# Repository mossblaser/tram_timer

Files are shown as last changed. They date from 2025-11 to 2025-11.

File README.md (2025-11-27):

Tram Timer
==========

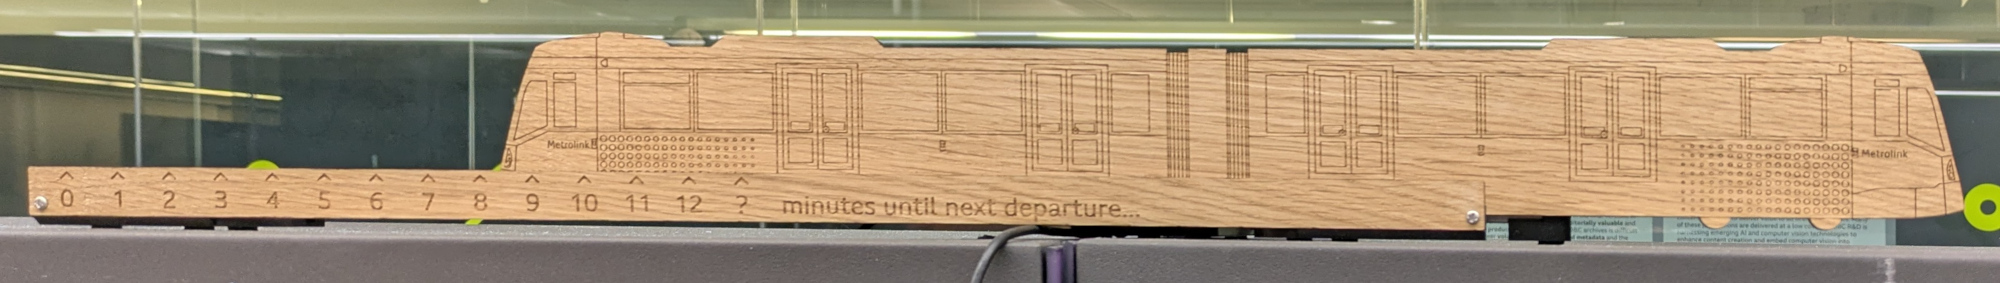
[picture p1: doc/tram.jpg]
A photo of the tram


A model tram which moves along its tracks to indicate how long until the next
departure from a [Manchester Metrolink](https://tfgm.com/ways-to-travel/tram)
tram stop.

Why?
----

There's nothing worse than heading to catch a tram from just outside the office
only to have just missed one, or find one isn't due for ages. Having an
indicator of when the next tram is due means you can always set off at just the
right moment.

This project is the successor to a simple [analogue gauge showing tram
departures I built some years ago](http://jhnet.co.uk/misc/trambox.jpg). Unlike
its predecessor, however, this one can be seen by the whole office.

Design
------

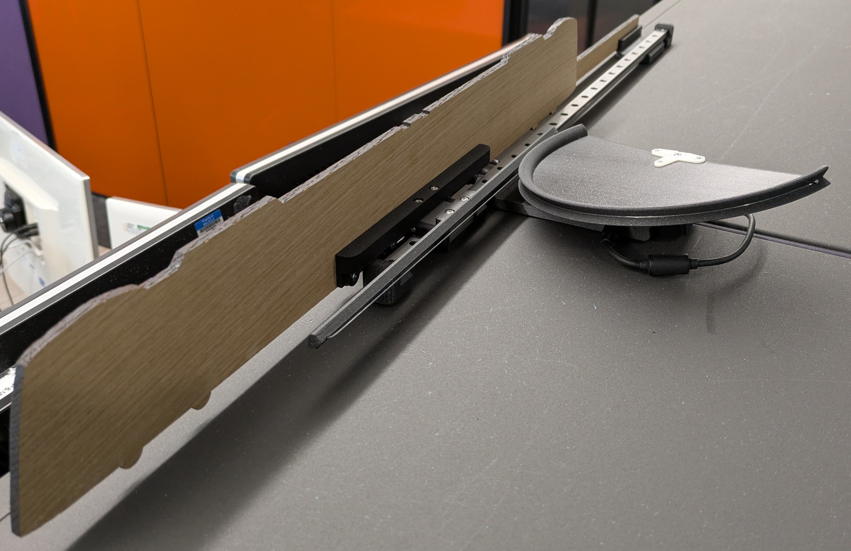
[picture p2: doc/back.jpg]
A photo of the back, showing the mechanism


The mechanism centres around a 600mm MGN12H linear rail (available from the
usual dubious suppliers). A laser cut tram rides along this rail propelled by a
standard RC servo driving a rack-and-pinion style linkage.

A Raspberry Pi Pico W microcontroller pulls Metrolink service data from the
[TFGM/BeeNetwork Metrolink Open Data
API](https://tfgm.com/data-analytics-and-insight/open-data-portal) via WiFi to
drive the servo.

Apart from the laser cut tram and linear rail, all other components are 3D
printed. M-series nuts, bolts and brass heat-set inserts connect everything
together.

### Mechanism

The servo and rack and pinion based mechanism was selected for its extreme
simplicity of implementation. With nothing more than 5v from the USB bus and a
3.3v PWM signal directly from a microcontroller, this setup gets you a
closed-loop absolutely-positioned linear actuator.

Rather than using toothed gears, two lengths of fishing line connect the rack
and pinion. This reduces the need for tight mechanical tolerances and makes
operation quieter.

The major downside of the rack and pinion approach is the additional space
taken up by the pinion wheel. Another limitation is that high resolution
movement accuracy is not typically possible given the slop and dead bands of
typical RC servos.

However, more compact or better performing options such as a belt-driven system
would be unjustifiably more complex to implement for relatively unimportant
gains.

### Firmware

The firmware is "the simplest thing that could possibly work". It's written in
[MicroPython](https://micropython.org/) because performance is utterly
irrelevant and microcontrollers have far too much RAM nowadays.

The only interesting quirk is that the Metrolink API returns status information
for every platform on the entire network in a single large JSON blob too large
to fit in RAM once deserialised. As a result, the firmware must incrementally
read and parse the structure.

For the benefit of future custodians of this device, details on flashing and
configuring the firmware can be found in
[firmware/README.md](./firmware/README.md)

### CAD

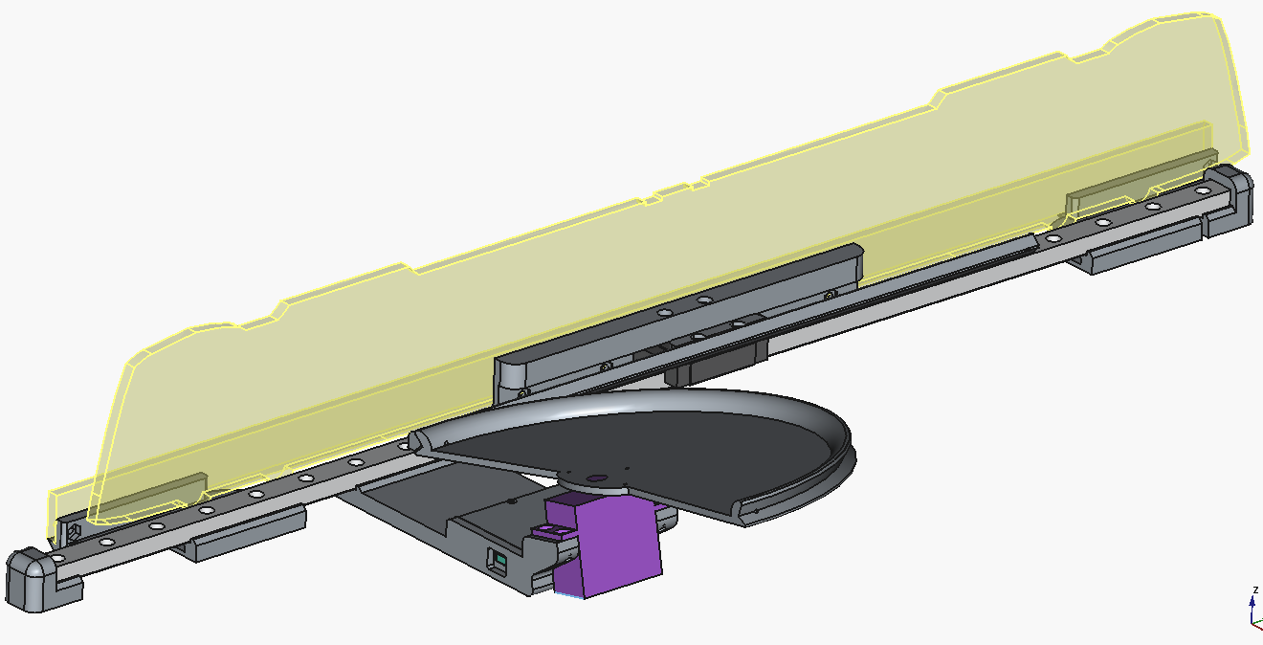
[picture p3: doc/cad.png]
FreeCAD screenshot


This project was my first using FreeCAD 1.0. After dismissing it as unusable
many years ago, I was delighted to discover the hype around FreeCAD 1.0 is
justified. It may be a long way behind its commercial counterparts but it is by
far the most powerful Open Source graphical 3D CAD tool I'm aware of.

2D CAD for the laser-cut tram was, of course, done in Inkscape. For
authenticity, I did most of the work whilst riding the tram.

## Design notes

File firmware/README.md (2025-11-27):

Firmware flashing and configuration
===================================

## Installing MicroPython

To use this firmware, a [MicroPython build for the Raspberry Pi Pico
W](https://micropython.org/download/RPI_PICO_W/) must be installed on the
device. I have tested with v1.26.1. If MicroPython is already installed,
there's likely no need to re-install it -- we just need to update our software.

## Copying the firmware

To copy the firmware onto the device you might wish to use
the [upyt](https://github.com/mossblaser/upyt) tool. Set the device name in
your environment like so:

```sh
export UPYT_DEVICE=/dev/ttyACM0
```

Before we copy anything across, the `config.py` file needs creating and
populating as indicated in `config.py.example`.

> [!NOTE]
> Unfortunately, TFGM/BeeNetwork are not handing out new API keys at the moment
> so you'll need to beg or borrow one.
>
> If you already have a device with an API key configured, make sure you note
> it down (e.g. by reading back the `config.py` file) -- with the key owner's
> permission, of course!
>
>     upyt cp :config.py .

We can fiddle with the `position_min_ns` and `position_max_ns` settings later
on.

Copy the firmware across to the device and reset to set it running:

```sh
upyt sync --reset path/to/firmware/
```

> [!TIP]
> Add the `--terminal` argument to start a serial terminal after the file sync
> is complete.

## Calibrating the servo

Servos can differ slightly in the range of PWM values they expect. To extract
the full range out of a servo, the `position_min_ns` and `position_max_ns`
values may need adjusting. To do this we'll use the MicroPython REPL.

Attach a serial terminal using:

```sh
upyt terminal
```

Since the firmware starts the watchdog timer, we'll need to perform a soft
reset and interrupt the firmware before the watchdog is started. To do this
press Ctrl+D to trigger a reset and then press Ctrl+C during the count-down to
the watchdog starting. You should drop into a Python REPL.

The `tram` object is an instance of the `Tram` class in [`tram.py`](./tram.py).
This is used to move the tram along the track. You can check the calibration by
manually running commands such as:

```python
>>> tram.move_to(4)  # Move to the four minute mark
```

If the spacing is right but everything is offset slightly you might be able to
adjust the position of the countdown board/platform by loosening the screws
attaching it to the linear rail and moving it along.

If the scale is off, you will need to adjust `position_min_ns` and
`position_max_ns`. This is a matter of trying PWM values by trial-and-error for
the '0' and '?' positions on the scale and setting `position_min_ns` and
`position_max_ns` respectively.

To control the servo, first turn it on:

```python
>>> tram._pwm.freq(50)
>>> tram._pwm.duty_ns(566_500)
>>> tram._pwm.init()
```

Then iteratively call `tram._pwm.duty_ns(...)` with new values until you've
determined the two endpoints.

Write the values into `config.py`, copy it onto the device and reset  (using
`upyt sync --reset path/to/firmware/`) and check the calibration again.

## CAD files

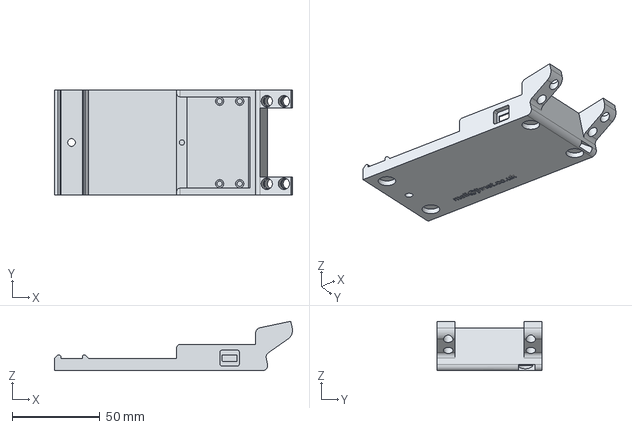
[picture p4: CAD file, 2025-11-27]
cad/3d_print/mechanism-Stand.step
135.5 x 60.0 x 28.2 mm

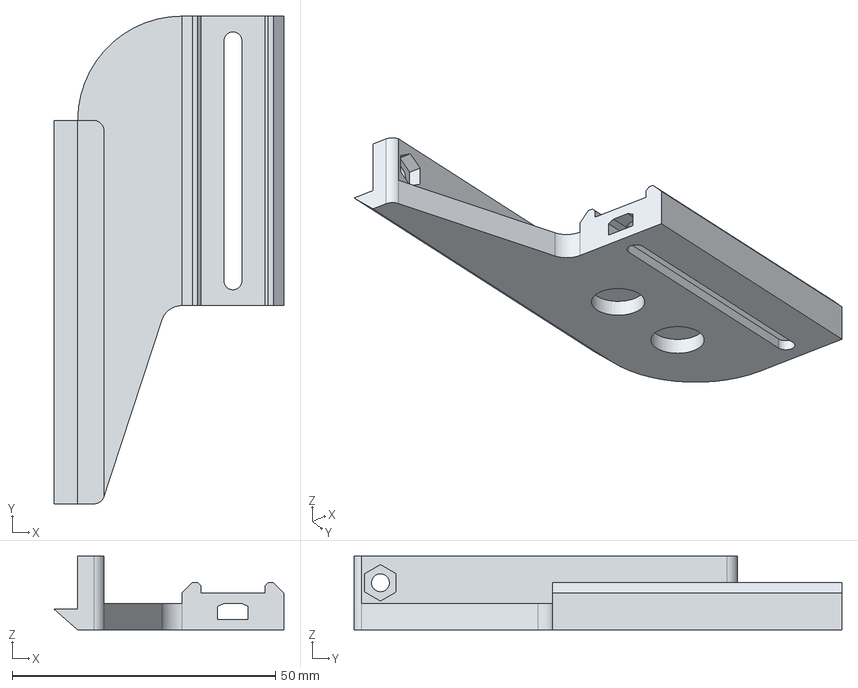
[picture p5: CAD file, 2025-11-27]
cad/3d_print/mechanism-CountdownBracketR.step
43.7 x 92.7 x 14.0 mm

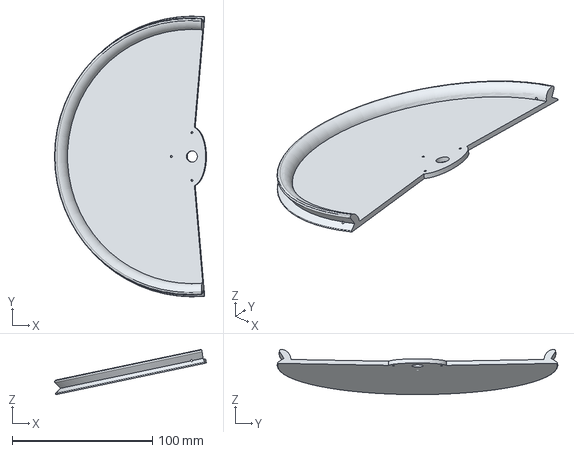
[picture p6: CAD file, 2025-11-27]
cad/3d_print/mechanism-Pinion.step
108.3 x 200.0 x 32.2 mm

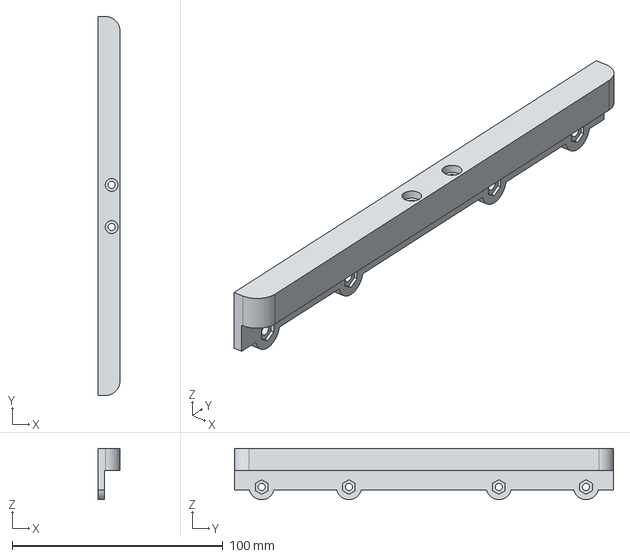
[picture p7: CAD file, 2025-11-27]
cad/3d_print/mechanism-TramCarriage.step
10.5 x 180.0 x 24.3 mm

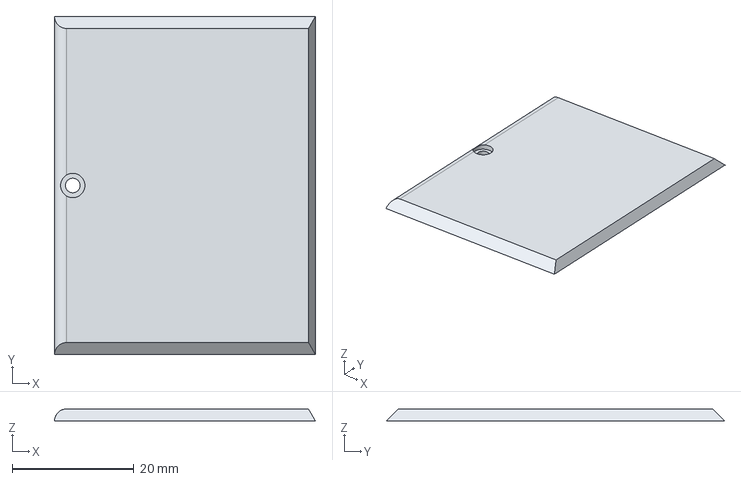
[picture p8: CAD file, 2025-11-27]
cad/3d_print/mechanism-ElectronicsLid.step
42.9 x 55.6 x 2.00 mm

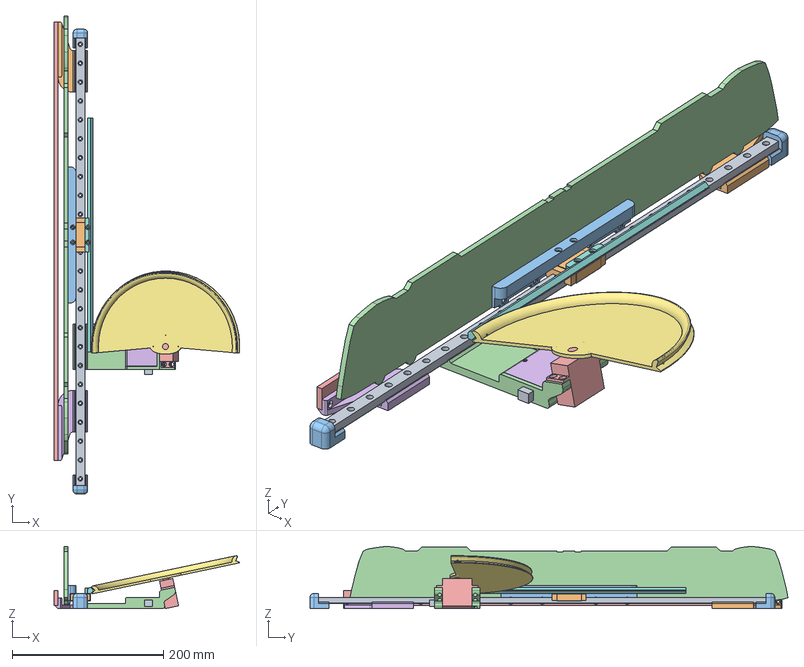
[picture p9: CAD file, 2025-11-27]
cad/3d_print/mechanism.FCStd
245.4 x 632.4 x 82.3 mm
Rail
Block
Foot x 2
Stand
Servo
ElectronicsLid
Pinion
Rack
PicoW
CountdownBracketL
TramCarriage
TramPlaceholder
CountdownPlaceholder
CountdownBracketR

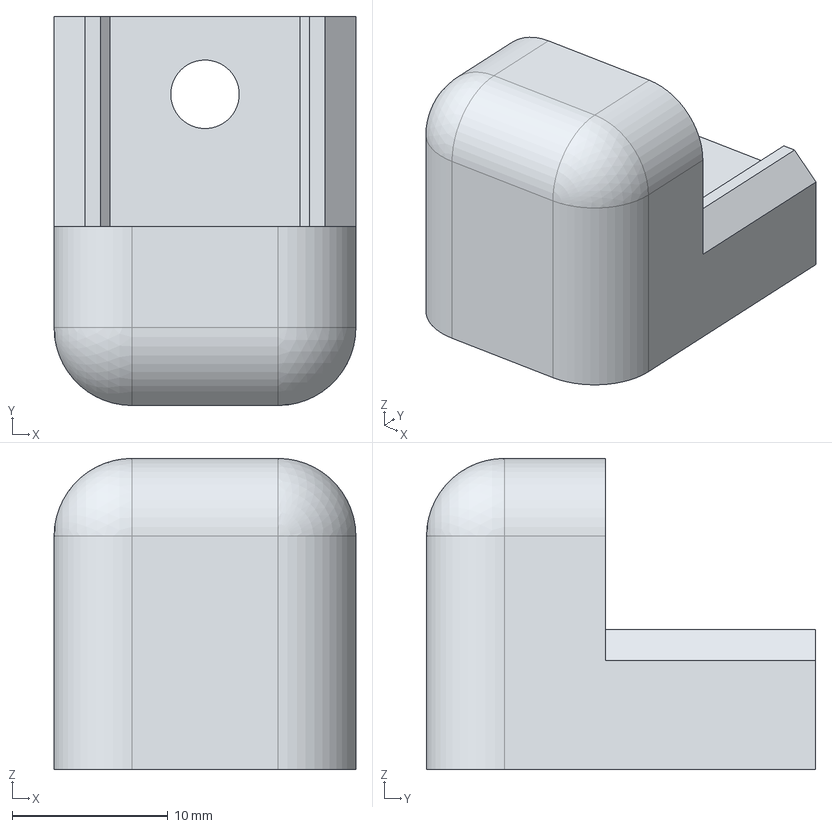
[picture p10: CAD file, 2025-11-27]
cad/3d_print/mechanism-Foot.step
19.4 x 25.0 x 20.0 mm

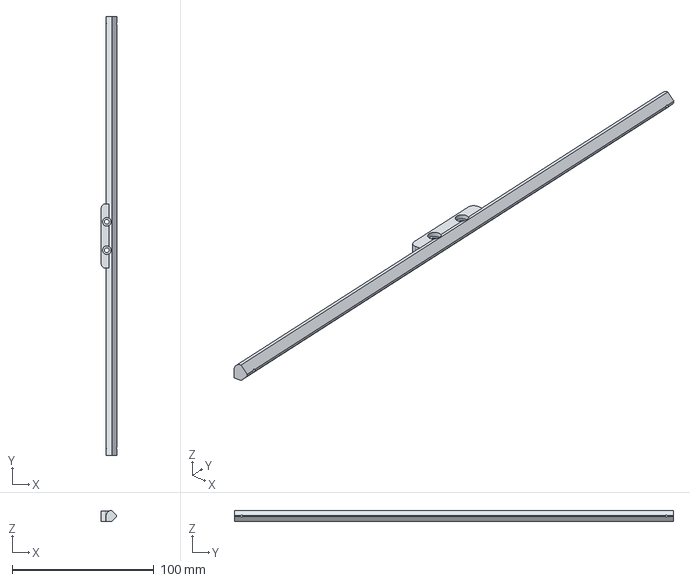
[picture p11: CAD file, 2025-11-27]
cad/3d_print/mechanism-Rack.step
11.0 x 310.0 x 8.00 mm

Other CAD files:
cad/3d_print/mechanism-CountdownBracketL.step

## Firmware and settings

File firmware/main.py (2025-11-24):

import time

from machine import Pin
import network

import watchdog
from tram import Tram
from metrolink_api import get_next_station_departure


if __name__ == "__main__":
    from config import *
    
    pin = Pin(28, Pin.OUT)
    tram = Tram(
        pin,
        position_min_ns=position_min_ns,
        position_max_ns=position_max_ns,
    )
    
    for t in range(10, 0, -1):
        print(f"Starting watchdog in {t}...")
        time.sleep(1)
    watchdog.feed()
    
    print("Connecting to WiFi...")
    nic = network.WLAN(network.WLAN.IF_STA)
    nic.active(True)
    nic.connect(wifi_ssid, wifi_key)
    
    while True:
        try:
            print("Looking up tram times...")
            next_departure = get_next_station_departure(
                station=station,
                excluded_destinations=excluded_destinations,
                api_key=api_key,
            )
            print("Next tram:", next_departure, "min")
            if next_departure is not None and 0 <= next_departure <= 12:
                tram.move_to(next_departure)
            else:
                tram.move_to(13)
            watchdog.feed()
        except Exception as e:
            print("Error:", e)
        finally:
            time.sleep(10)

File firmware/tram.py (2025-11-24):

"""
Implements control of the servo which moves the model tram.

Example:

    >>> from tram import Tram
    >>> tram = Tram(Pin(22))
    >>> tram.move_to(0)
    >>> tram.move_to(5)
    >>> tram.move_to(12)
"""

import math
import time

from machine import Pin, PWM


def sinusoidal_ease(p):
    """
    Simple sinusoidal easing function.
    """
    return -(math.cos(math.pi * p) - 1) / 2

class Tram:
    """
    Controls the movement of the servo which moves the model tram along its
    track.
    
    The tram can move between a defined number of discreete steps defined by
    the 'steps' parameter. Positions are numbered from 0 to steps-1
    (inclusive).
    """

    _pwm: PWM
    
    # The PWM period (in ns) corresponding to minimum/maximum positions
    _position_min_ns: float
    _position_max_ns: float

    # The number of equally-spaced discrete positions the tram can take along
    # its track
    _steps: int
    
    # The last set position of the tram (in steps)
    _position: int | None
    
    # The duration over which a full-scale movement should be performed (in
    # seconds)
    _full_scale_duration: float
    
    # The easing function to use for movements (float -> float)
    _ease: "Callable"

    def __init__(
        self,
        pin: Pin,
        position_min_ns: float = 566_500,
        position_max_ns: float = 2_200_000,
        steps: int = 14,
        full_scale_duration: float = 4.0,
        ease = sinusoidal_ease,
    ) -> None:
        """
        Params
        ------
        pin : Pin
            The pin the servo control pin is attched to.
        position_min_ns : int
        position_max_ns : int
            The servo PWM 50 Hz 'high' period in nanoseconds for its minimum
            and maximum extents. That is, at positions 0 and steps-1.
        steps : int
            The number of discrete positions the tram can be in. This should
            correspond with the number of marks written on the tram tracks.
        full_scale_duration : float
            The number of seconds to take to move between the two most extreme
            positions. Shorter moves will be made over proportionally shorter
            durations.
        ease : function(ratio) -> value
            An easing function to apply to the movements of the tram. Should
            take and return a float between 0.0 and 1.0.
        """
        
        self._pwm = PWM(pin)
        
        # Ensure PWM generator is off initially to prevent the servo buzzing or
        # movement
        self._pwm.deinit()
        
        self._position_min_ns = position_min_ns
        self._position_max_ns = position_max_ns
        
        self._steps = steps
        
        self._position = None
        
        self._full_scale_duration = full_scale_duration
        self._ease = ease
    
    def _position_to_ratio(self, position: int) -> float:
        return position / (self._steps - 1)
    
    def _position_to_ns(self, position: int) -> float:
        full_range = self._position_max_ns - self._position_min_ns
        return self._position_min_ns + full_range * self._position_to_ratio(position)
    
    def move_to(self, position: int) -> None:
        """
        Move to the provided position (i.e. step number). Blocks whilst the
        servo moves.
        """
        # NB: Special handling is required for our first move since the servo
        # could be in an unknown position on startup. Rather than tweening
        # between first/last position, we instead just give the servo a long
        # time to settle on the desired position.
        first_movement = False
        if self._position is None:
            self._position = position
            first_movement = True
        
        # Scale the duration of the movement based on how far we have to move
        change_steps = abs(self._position - position)
        change_ratio = self._position_to_ratio(change_steps)
        duration_ms = (self._full_scale_duration * change_ratio) * 1000
        
        position_start_ns = self._position_to_ns(self._position)
        position_end_ns = self._position_to_ns(position)
        
        self._pwm.freq(50)
        self._pwm.duty_ns(round(position_start_ns))
        self._pwm.init()
        
        # Move from the previous to new position
        start_ms = time.ticks_ms()
        while True:
            ellapsed_ms = time.ticks_diff(time.ticks_ms(), start_ms)
            if ellapsed_ms >= duration_ms:
                break
            
            p = self._ease(ellapsed_ms / duration_ms)
            
            self._pwm.duty_ns(
                round(
                    position_start_ns +
                    ((position_end_ns - position_start_ns) * p)
                )
            )
            time.sleep_ms(round(1000 / self._pwm.freq()))
        
        # Give the servo some extra time to settle on its final position.
        self._pwm.duty_ns(round(position_end_ns))
        if first_movement:
            # Allow time for a possibly large movement at high speed during
            # initial move
            time.sleep_ms(1000)
        else:
            time.sleep_ms(100)
        
        # Turn off the servo to prevent buzzing
        self._pwm.deinit()
        
        self._position = position

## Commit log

2025-11-27 Add CAD files
    [mechanism-CountdownBracketL.step, mechanism-CountdownBracketR.step, mechanism-ElectronicsLid.step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]
2025-11-27 Fix CAD screenshot in README
